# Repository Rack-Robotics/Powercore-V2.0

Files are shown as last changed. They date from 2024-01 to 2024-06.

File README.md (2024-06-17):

# Powercore V2.0

Powercore Front View 

The Powercore V2.0 is an open-source wire EDM (electrical discharge machining) power supply developed by Rack Robotics. It aims to provide a cost-effective and easily replicable solution for wire EDM enthusiasts and professionals. The project includes detailed electrical schematics, firmware, and CAD models. This EDM power supply (spark generator) is intended to be used on custom wire EDM and plunge EDM machines. 

This porject is open-source, to encourage collaboration and innovation within the wire EDM community.

## Powercore V2.0 Specifications

| Specification | Value |
|---|---|
| Typical Input Power | 200 Watts |
| Input Voltage | 90-264 VAC |
| Input Frequency | 47-63 Hz |
| Output Voltage | 65 VDC |
| Power Efficiency | Up to 90% |
| PSU Enable Port Voltage Input | 5-36 V |
| Physical Dimensions (XYZ) | 97 x 224 x 79.5 (mm) |

## Features 
- Firmare optimized for stable wire EDM opperation
- Up to 180 Watts EDM Power Output (Output Port)
- Up to 18 mJ per EDM spark
- 2 KHz EDM cutting with factory firmware
- Dual-core RP2040 Microcontroller up to 133 MHz (USB Port)
- Real-Time Current Sensing Telemetry (AMP Port) 
- Real-Time Spark Ignition Telemetry (ALRT Port) 
- External PSU Enable Safety Feature

## FAQ
**Can this cut X material?**

EDM can errode any conductive material. The rate of EDM (Electrical Discharge Machining) machining, also known as spark erosion, is significantly influenced by the thickness, melting point, and density of the material being worked on. Thicker materials generally require more time to erode due to the increased volume that must be removed. Materials with a higher melting point also slow down the machining rate as more energy is required to melt and vaporize the material at the spark point. Additionally, denser materials resist erosion more effectively, requiring more discharge energy to achieve the same material removal rate as less dense materials. Example feedrates are provided bellow, for 0.3 mm diameter zinc-coated, hard brass wire.

| Material | Example Feedrate |
|---|---|
| 3 mm Aluminum | 10 - 28 mm/min |
| 19 mm Aluminum | 1.6 - 4.4 mm/min |
| 4.75 mm Aluminum | 6 - 17 mm/min | 

**Can the Powercore V2.0 be used for sinker/plunge EDM?**

Yes. Gap control is highly recommended for sinker/plunge applications. In plunge/sink EDM, gap control is critical for maintaining machining stability. The gap, or spark gap, is the small space between the electrode and the workpiece. Proper gap control ensures consistent sparking conditions, preventing short circuits and arcing that can damage the workpiece and electrode. It also aids in efficient debris removal, cooling, and flushing of the dielectric fluid, which are essential for maintaining a smooth surface finish and achieving high-accuracy machining. Without precise gap control, the machining process can become unstable, leading to poor-quality results and increased wear on the electrodes. The Powercore V2.0 has a current sense and short alert output port to assist the user in thier implementation. 

## IO Ports

| Port | Description |
| --- | --- |
|**POWER** | The Powercore V2.0 outputs EDM waveforms through an 8-position Molex Micro-Fit 3.0 connector. The included output cable is 1 meter long and rated for 30 cycles. This cable consists of four twisted pairs to significantly reduce electromagnetic emissions. For more information about twisted wires and their benefits, refer to the best practices section.|
|**ALRT** | The Powercore V2.0 provides digital telemetry on the spark ignition rate via the ALRT port. The spark ignition rate, defined as the ratio of 'observed discharges' to 'possible discharges'. The spark ignition rate is a key indicator of feedrate efficiency. A low rate suggests the feedrate can be increased, while a high rate indicates an excessive feedrate or a short circuit. Telemetry is reported as a PWM duty cycle, which can be read by a control board or microcontroller. This port enables closed-loop feedrate control, ensuring optimal material removal. An ignition rate of approximately 80% has been observed to be optimal.|
|**AMP**| The Powercore V2.0 provides analog telemetry via the on-board current sensor (U17A, LMV358AIDGKR, output shunt). It is mapped to between 0V and 3.3V, at a rate of 12 mV/A. This may be used for closed-loop feedback control and debugging. |
|**EN**| The Powercore V2.0 features an "enable port" that ensures safety by requiring activation before the device outputs EDM waveforms. When the Powercore is plugged in, it remains inactive until the enable port receives a DC voltage between **5V and 36V**. This port draws minimal current. The enable port can be connected to GPIO, motor, heater, or LED ports on a 3D printer or CNC control board, or controlled manually with a switch. *To prevent damage*, avoid disconnecting the main AC power while the enable port is active.|
|**USB**| A type-C USB port provides communication with the on-board RP2040 micronctroller and flash memory. Pressing the reset button (the pin-hole located between the ‘AMP’ and ‘EN’ ports) during power-up initiates the USB bootloader mode, allowing access to the flash memory. When the reset button is held down while powering up, the RP2040 enters a special state where it presents itself as a mass storage device to a connected computer. This enables users to drag and drop firmware files directly into the flash memory, facilitating easy updates and modifications without needing additional programming tools or interfaces.|

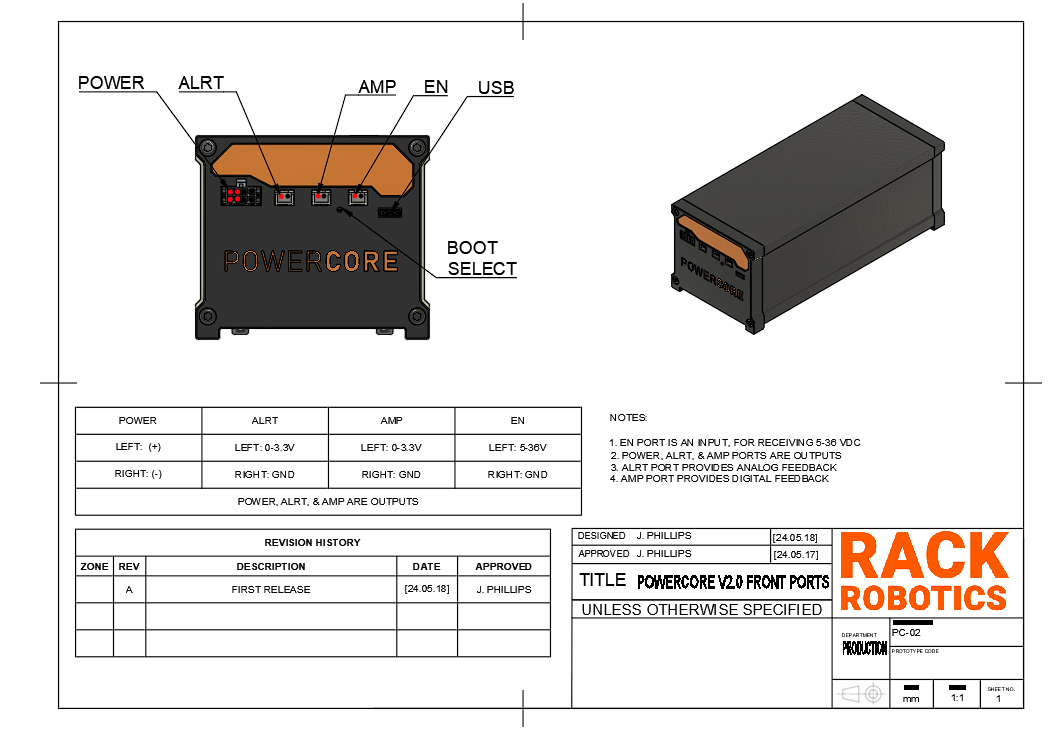
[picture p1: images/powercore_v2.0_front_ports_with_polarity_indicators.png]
Powercore Front View


**Best_Practices**

- Avoid short circuits. A short circuit occurs when the POWER port outputs short together. This may happen if wiring is incorrect, or the cutting electrode collides with the work. A prolonged short circuit can damage the Powercore.
- Twist the output power cable pairs together. Twisting the positive and negative output conductors together dramatically reduces EMI, and improves the cutting efficiency of the device. Output cables come twisted from Rack Robotics.
- When integrating the Powercore V2.0 into a wire EDM build, ensure that the EN port fails to an off default state during machine shutoff.
  
⚠ Avoid touching the electrodes and workpiece during operation to prevent exposure to high-voltage DC (65V). Additionally, individuals with pacemakers or similar medical devices should not operate the Powercore, as the high-voltage environment could interfere with their functionality. 

# Hardware Overview

The Powercore V2.0 contains a custom SMPS and motherboard. The internal SMPS is rated for 300 W typical and 550 watts peak, and accepts a range of AC voltages and frequencies. The SMPS provides 72 VDC to the motherboard, via the motherboard input supply connector (J1). The motherboard converts the steady 72 VDC input power, into pulsed high-current DC power, which is suitable for EDM.

**Theory of Operation**

The Powercore V2.0 motherboard delivers parametric pulsed DC through the repeated charging and discharging of a 32.9 µF capacitor bank. Efficient and rapid capacitor charging is achieved via a [peak current-mode control](https://www.ti.com/lit/ab/sboa187e/sboa187e.pdf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) (PCMC) *charger stage*. The onboard RP2040 *microcontroller* monitors the capacitor voltage and adjusts the PCMC charger parameters accordingly. When an output pulse is needed, the RP2040 discharges the capacitor bank through the MOSFET-driven *output stage* into the POWER port. This design allows for precise control over the EDM output pulse parameters: on-time, off-time, and peak voltage.

⚠ Adjustment of the firmware, including the on-time, off-time, and peak-voltage, may lead to damage of the PCMC switching converter. Do so at your own risk. 

**Motherboard**

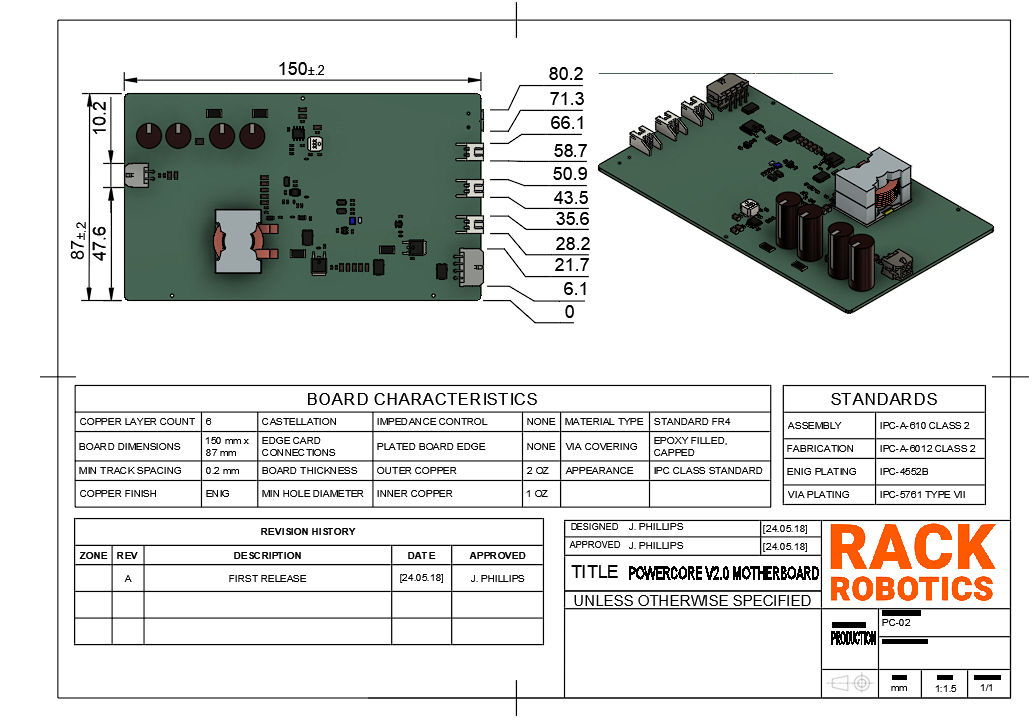
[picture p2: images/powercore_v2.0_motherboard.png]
Powercore Front View


The motherboard contains multiple functional blocks: 

- RP2040 Microcontroller with 16Mbit of FLASH Memory
- EMI Filter
- 72 VDC to 12 VDC Buck Converter
- 12 VDC & 5 VDC LDO
- Peak Current Detector
- Limit PWM Filter
- V_SENSE Scaler + Filter
- Peak Capacitor Voltage Trigger
- Constant Current PWM Generator
- Constant Current Limit Compensator & Slope Generator
- Output Curretn Sensor
- Charger Power Stage
- Output Stage

## Firmware Overview
Work in Progress

## Safety

DANGER The Powercore V2.0 operates at a potentially hazardous voltage of 65 - 72 VDC, and supplies high-power waveforms

Improper use of the Powercore can increase radiated emission levels. These intrinsic properties of EDM necessitate operator care and supervision. Touching the workpiece or electrode(s) during EDM operation exposes the may expose the user to 65 - 72 VDC high-voltage. Individuals with pacemakers or similar medical devices should not operate the Powercore, as the high-voltage environment could interfere with their functionality. Ensure that proper measures are taken against EMI. Routing of EDM power through unshielded/twisted cables not recommended. Unshielded/twisted cables function as antennas, which will radiate emissions into the nearby 

## 6. Legal & License

Shield: [][cc-by-nc]

This work is licensed under a
[Creative Commons Attribution-NonCommercial 4.0 International License][cc-by-nc].

[][cc-by-nc]

[cc-by-nc]: https://creativecommons.org/licenses/by-nc/4.0/
[cc-by-nc-image]: https://licensebuttons.net/l/by-nc/4.0/88x31.png
[cc-by-nc-shield]: https://img.shields.io/badge/License-CC%20BY--NC%204.0-lightgrey.svg

You are free to:
- Share — copy and redistribute the material in any medium or format
- Adapt — remix, transform, and build upon the material

Under the following terms:
- Attribution — You must give appropriate credit, provide a link to the license, and indicate if changes were made. You may do so in any reasonable manner, but not in any way that suggests the licensor endorses you or your use.
- NonCommercial — You may not use the material for commercial purposes.

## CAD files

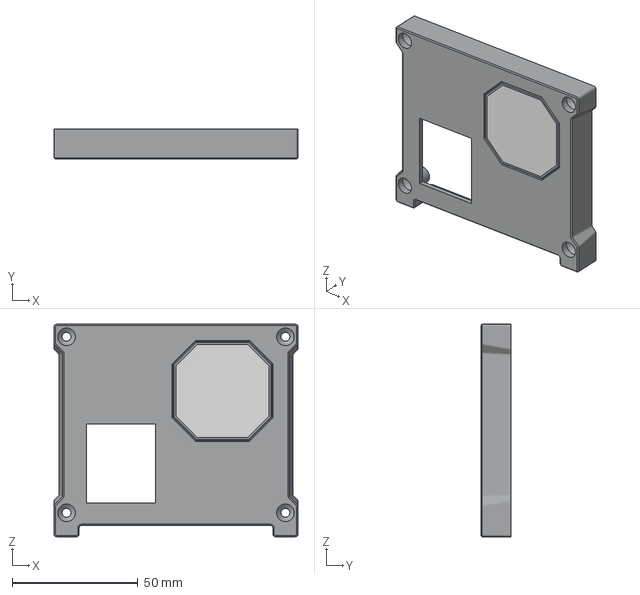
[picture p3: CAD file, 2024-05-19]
Powercore-V2.0 CAD/Back Panel v18.3mf
97.0 x 12.0 x 84.5 mm

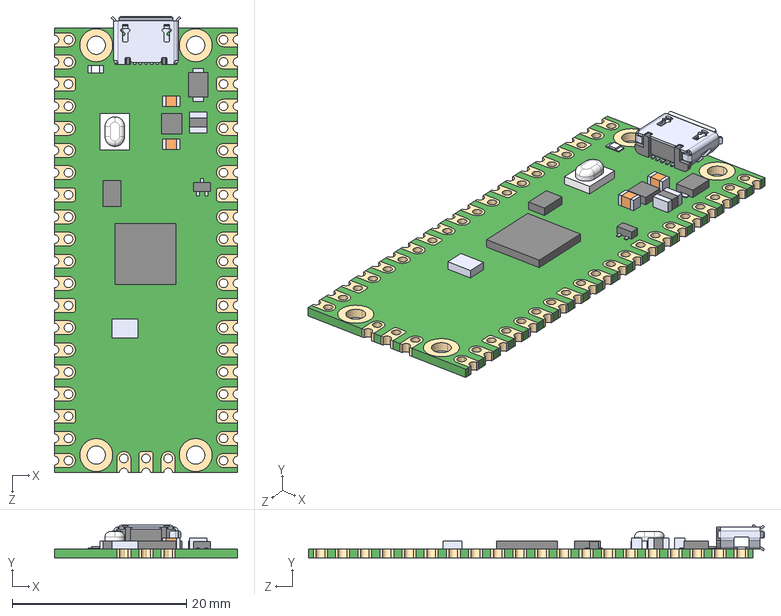
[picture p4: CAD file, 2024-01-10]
Powercore-V2.0 Motherboard/KiCAD/KiCAD Libraries/3dmodels/MCU_MODULES/SC0915.step
21.0 x 3.73 x 52.3 mm

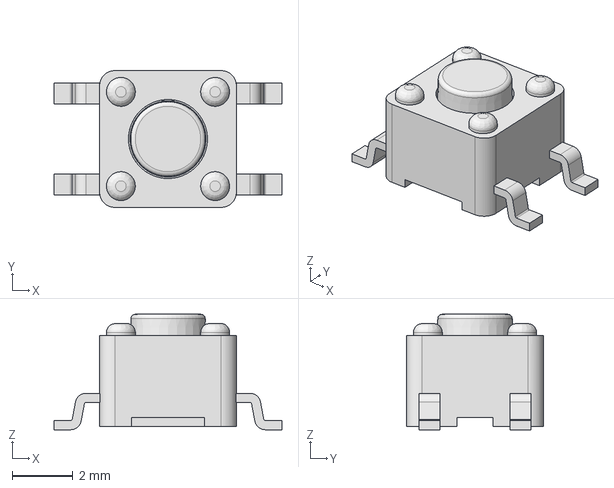
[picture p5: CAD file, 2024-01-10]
Powercore-V2.0 Motherboard/KiCAD/KiCAD Libraries/3dmodels/SWITCHES/TL3305AFxxxxG.stp
7.50 x 4.50 x 3.80 mm

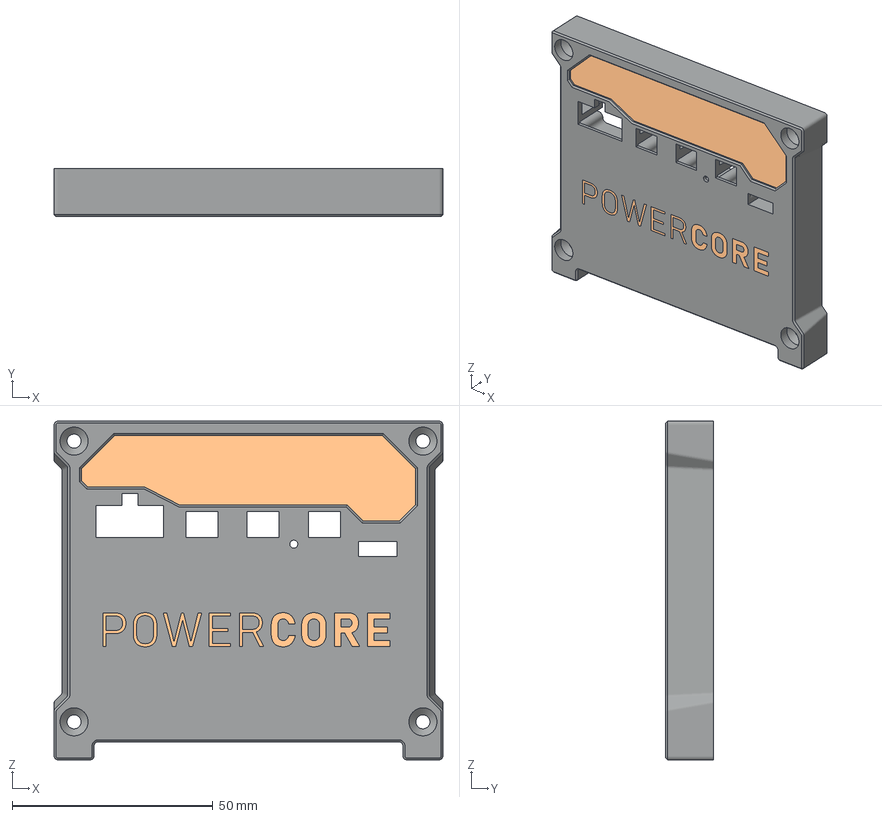
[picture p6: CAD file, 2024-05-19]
Powercore-V2.0 CAD/Front Panel v45.3mf
97.0 x 12.0 x 84.5 mm

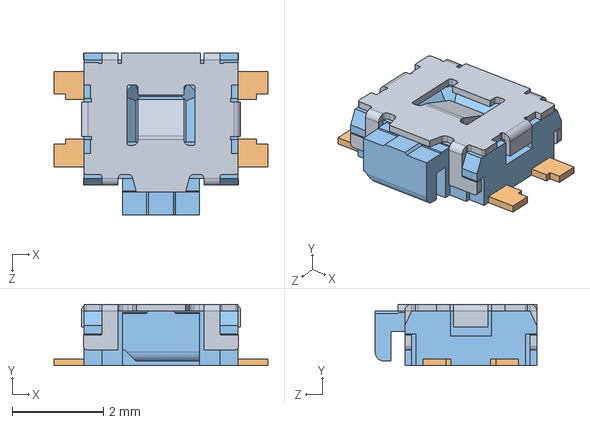
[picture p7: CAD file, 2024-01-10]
Powercore-V2.0 Motherboard/KiCAD/KiCAD Libraries/3dmodels/SWITCHES/EVQ-P7A01P.step
4.70 x 1.35 x 3.55 mm

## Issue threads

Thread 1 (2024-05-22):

Please add a EEVblog discussion thread

myjtag, 2024-05-22:
Hi
I highly recommend that you make a thread on EEVblog  forum, because there are lot's of interaction and highly skilled engineers there, to contribute and give feedback, Also I recommend you choose a better equipped MCU with SMPS control peripherals like STM32G431CBT6 which is affordable  enough and have lot's of great peripherals for controlling Advanced SMPS circuits. like ADC, DAC, Op-amp , comparator and Cordic engine

John-RackRobotics, 2024-05-29:
While I am a fan of the EEVblog YouTube channel, I do not frequent the forum. For our application, we do not require the STM32G431CBT6. We are happy with the RP2040 for the Powercore V2.0.

myjtag, 2024-05-30:
I highly recommend making a thread there, there is a hug and very active community there, they would help and contribute a lot.

Closed 2024-05-30.

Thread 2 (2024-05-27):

Is description of U2 in BOM correct

alberto-simoes, 2024-05-27:
Hi just checking the description of U2 in the BOM should read RP204... and not what it shows currently SC0914?

Apologies if i've misunderstood something here.

John-RackRobotics, 2024-05-29:
SC0914(13) is the original manufacturer part number for the RP2040 MCU, produced by Raspberry Pi.

Closed 2024-05-29.

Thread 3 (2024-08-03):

it stay in boot from flash mode

atmelletje, 2024-08-03:

atmelletje, 2024-08-03:
I build the board according to your designs, I don't have to push the boot button as it stays in boot mode. I used the MCU from an rp pico. all other parts are new. I meassure 3.25v at CLR pin 1. boot switch removed makes also no difference.

atmelletje, 2024-08-03:
that problem is solved. it was a fake/broken Flash chip.

Closed 2025-05-05.

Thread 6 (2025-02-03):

How to connect the internal circuit board of powercore V2

Logan147, 2025-02-03:
Thank you for your open source, sir, you are a genius！！！
Below is my question
1. Does powercore V2 need a resistor board like the V1 version, and how to connect the various internal circuit boards?
2. Can you provide a further detailed wiring diagram?

Logan147, 2025-02-03:
For example, how to connect the SMP power supply to the motherboard and the cooling fan?

Logan147, 2025-02-03:
For example, how to connect the SMPS power supply to the motherboard and the cooling fan?

Logan147, 2025-02-07:
ok, i got it.

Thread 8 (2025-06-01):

Control stage

hinell, 2025-06-01:
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

First of all: thanks for great project. I'm trying to figure out what these two OP-amps are doing in control stage. Why no output? Where I can read more about this?

Is this paper on [Current Mode Control in Switching Power Supplies](https://www.ti.com/lit/ab/sboa187e/sboa187e.pdf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) relatd to the the said op-amps?

Thanks!

Closed 2025-06-14.

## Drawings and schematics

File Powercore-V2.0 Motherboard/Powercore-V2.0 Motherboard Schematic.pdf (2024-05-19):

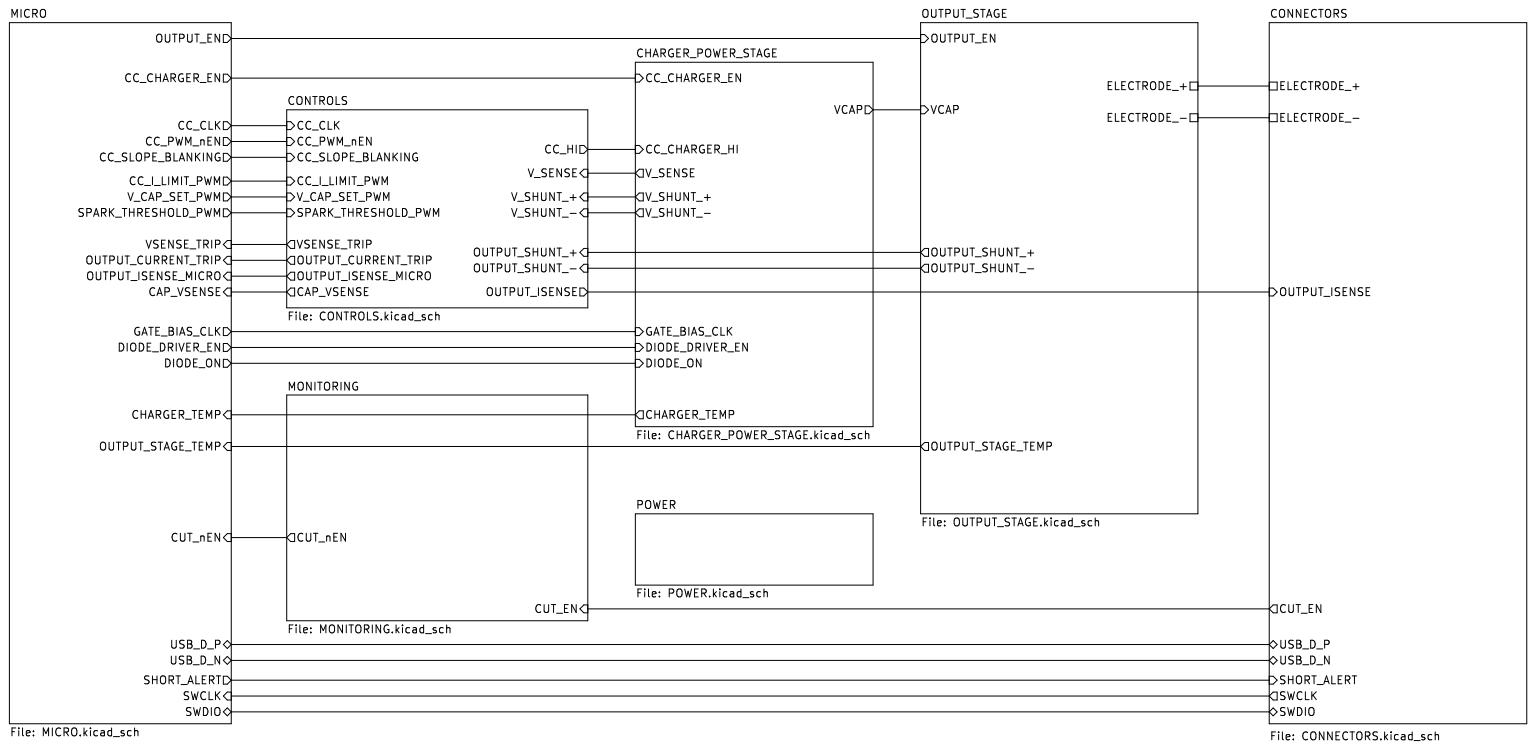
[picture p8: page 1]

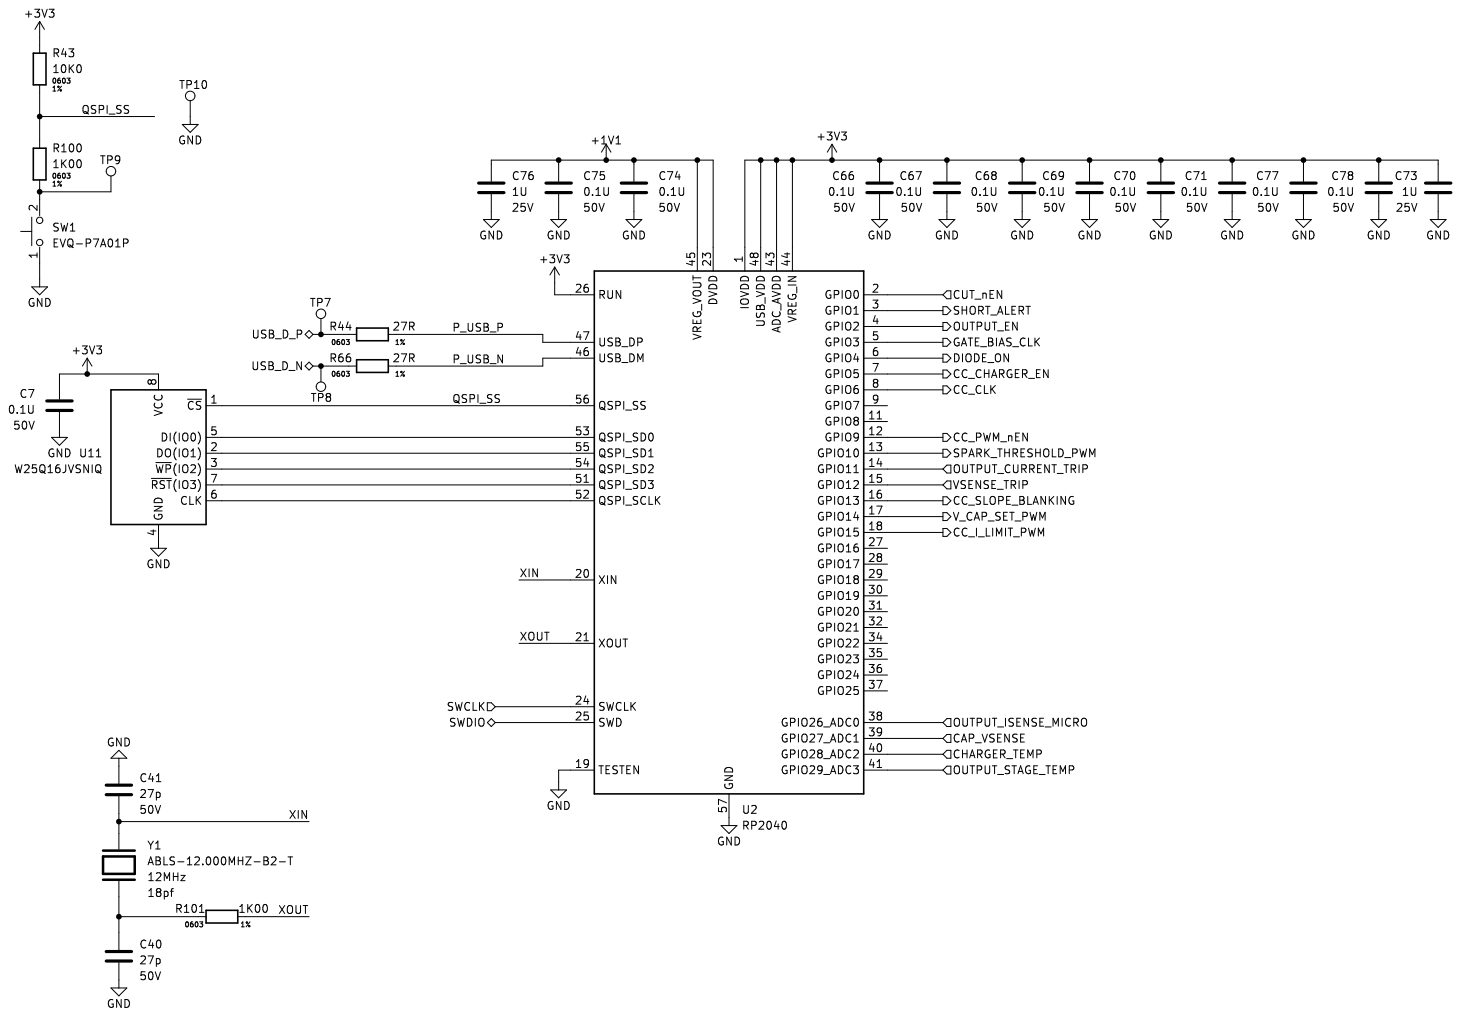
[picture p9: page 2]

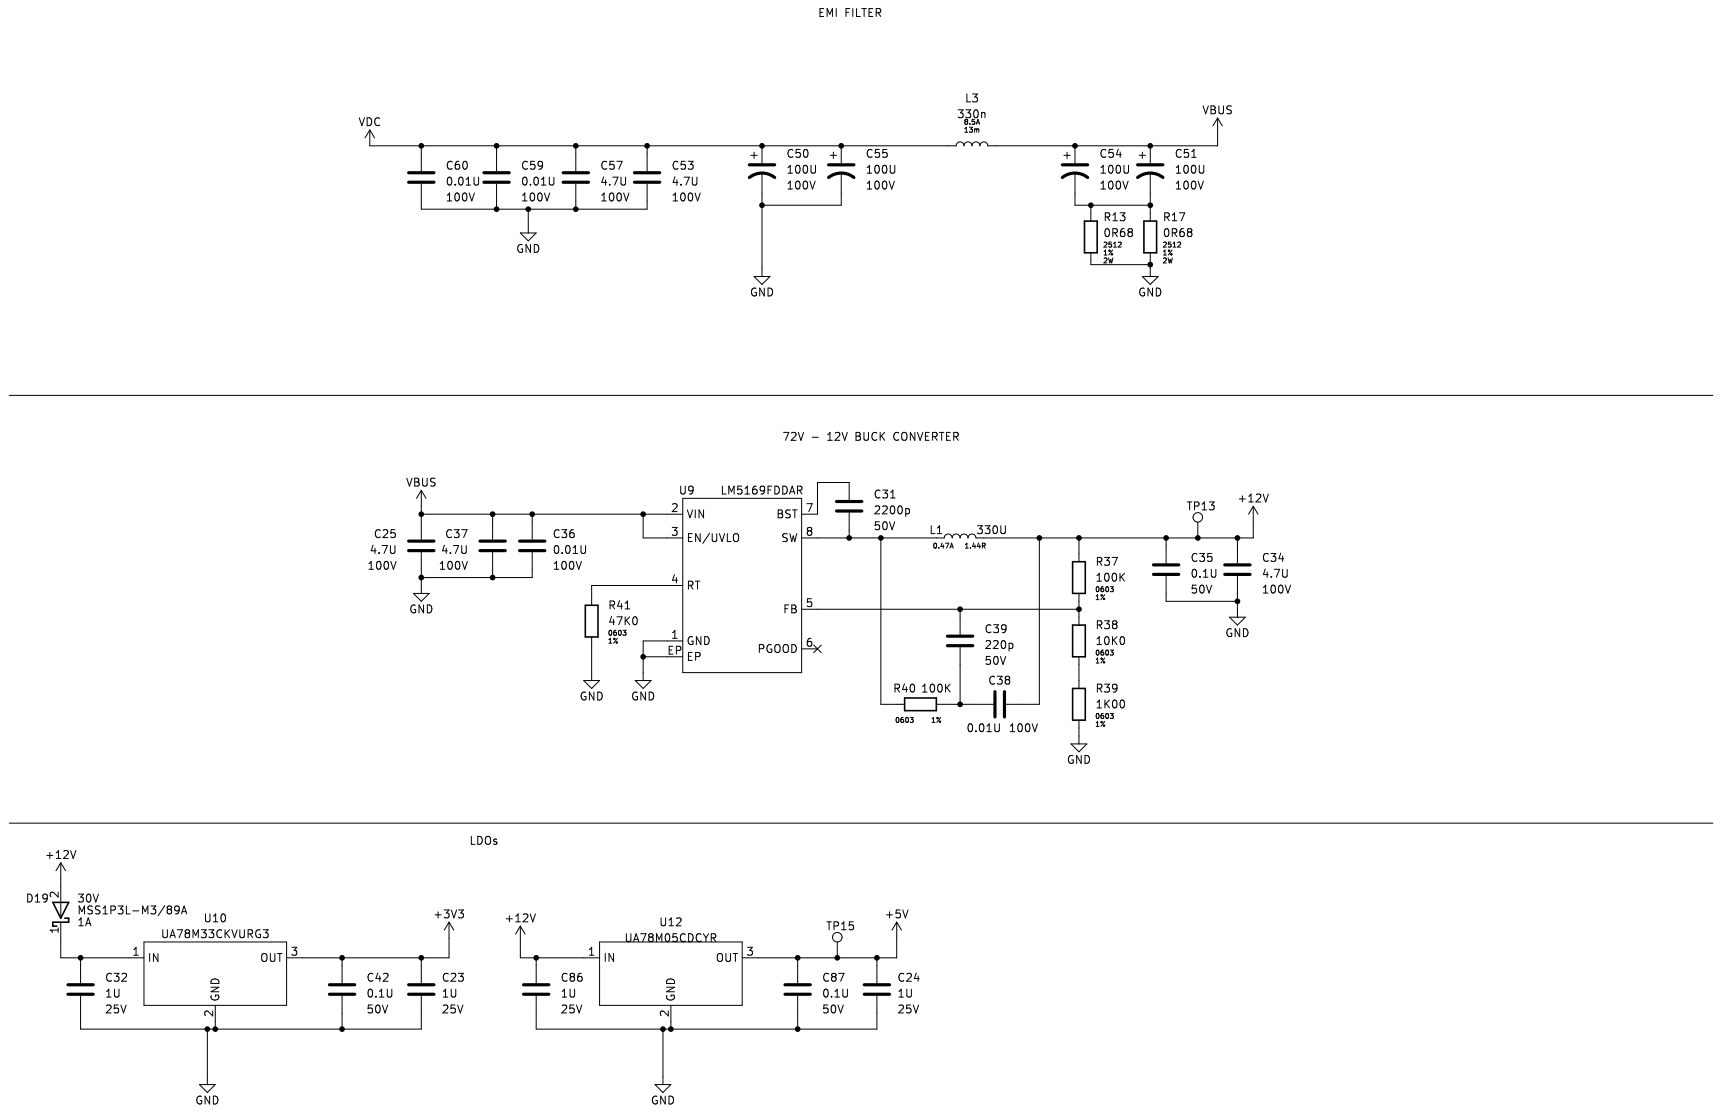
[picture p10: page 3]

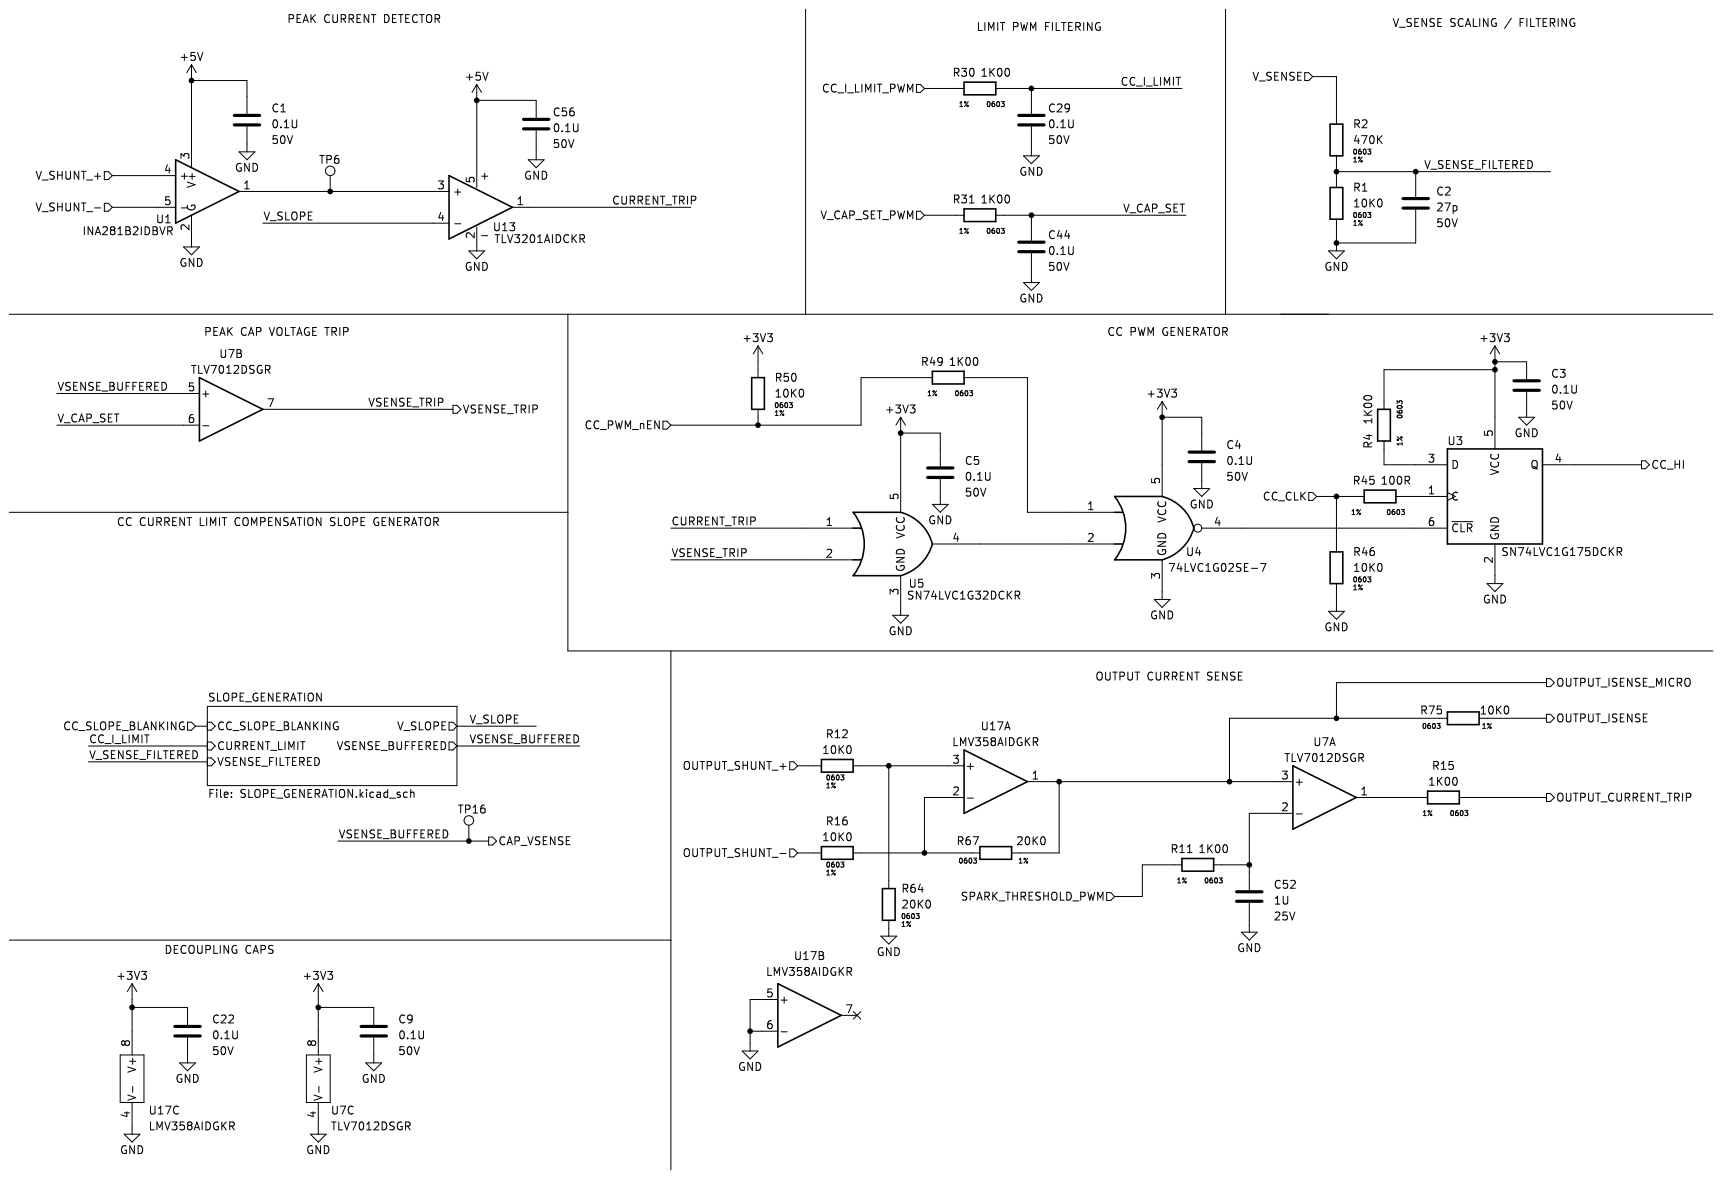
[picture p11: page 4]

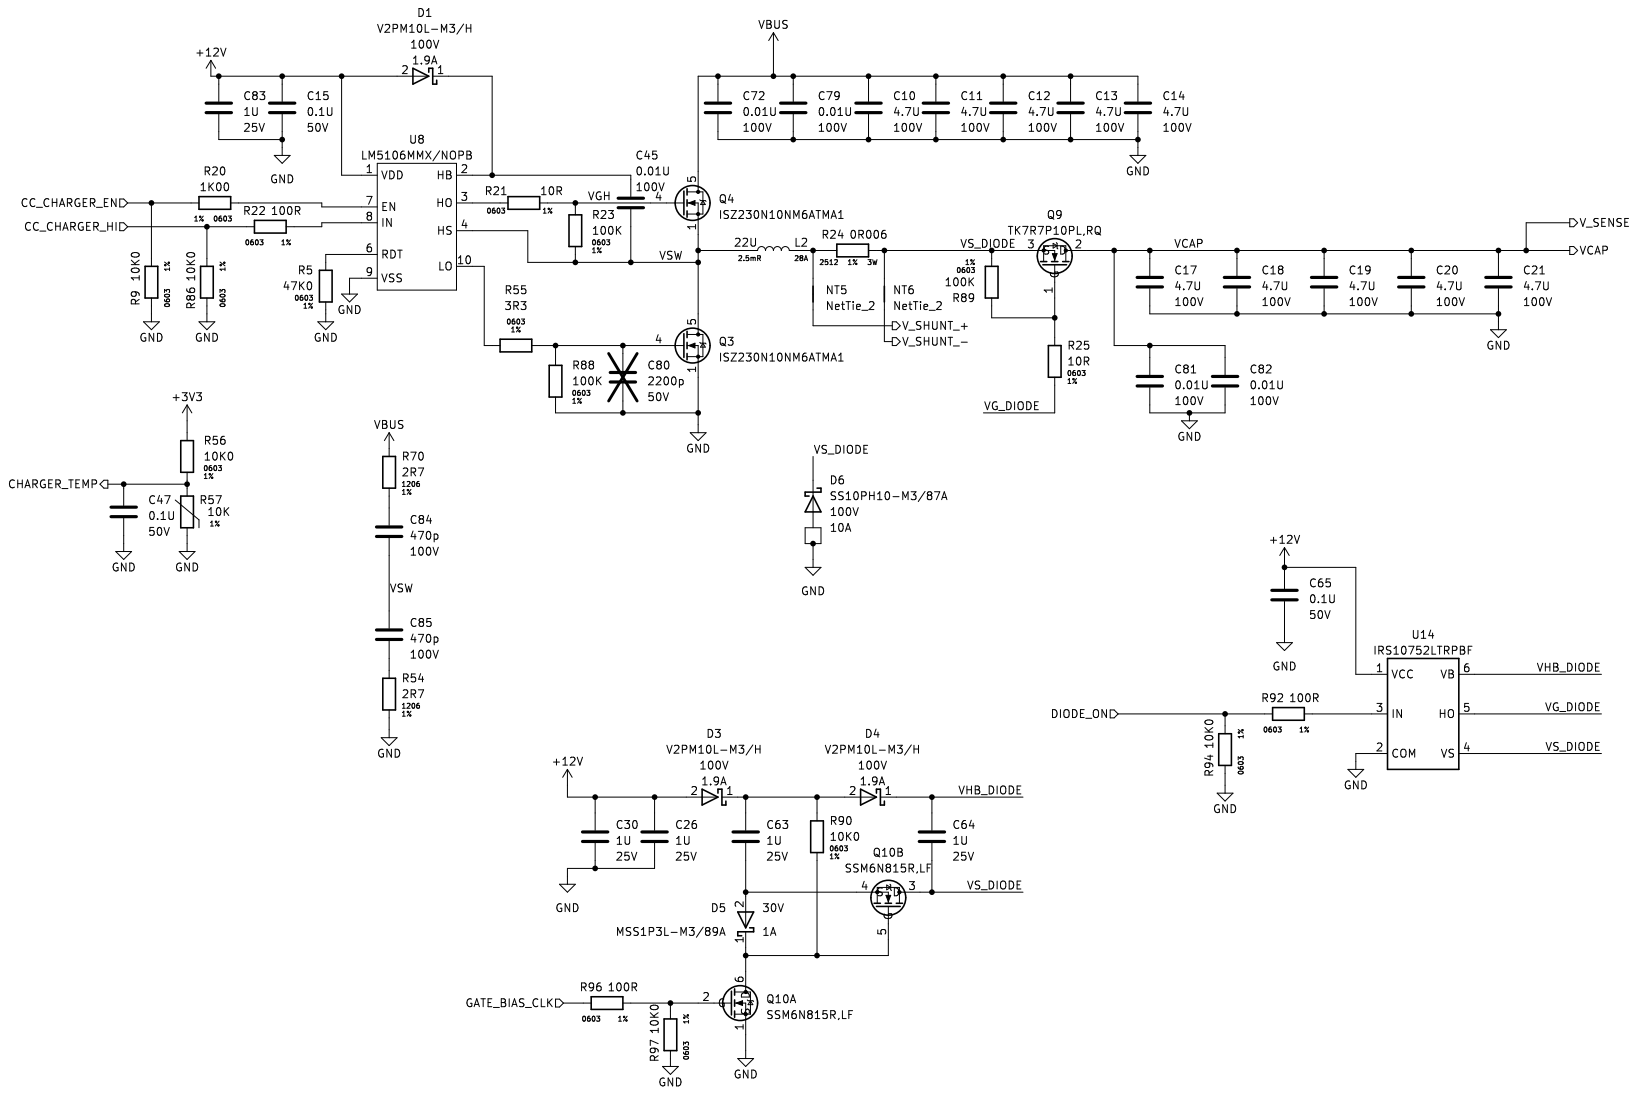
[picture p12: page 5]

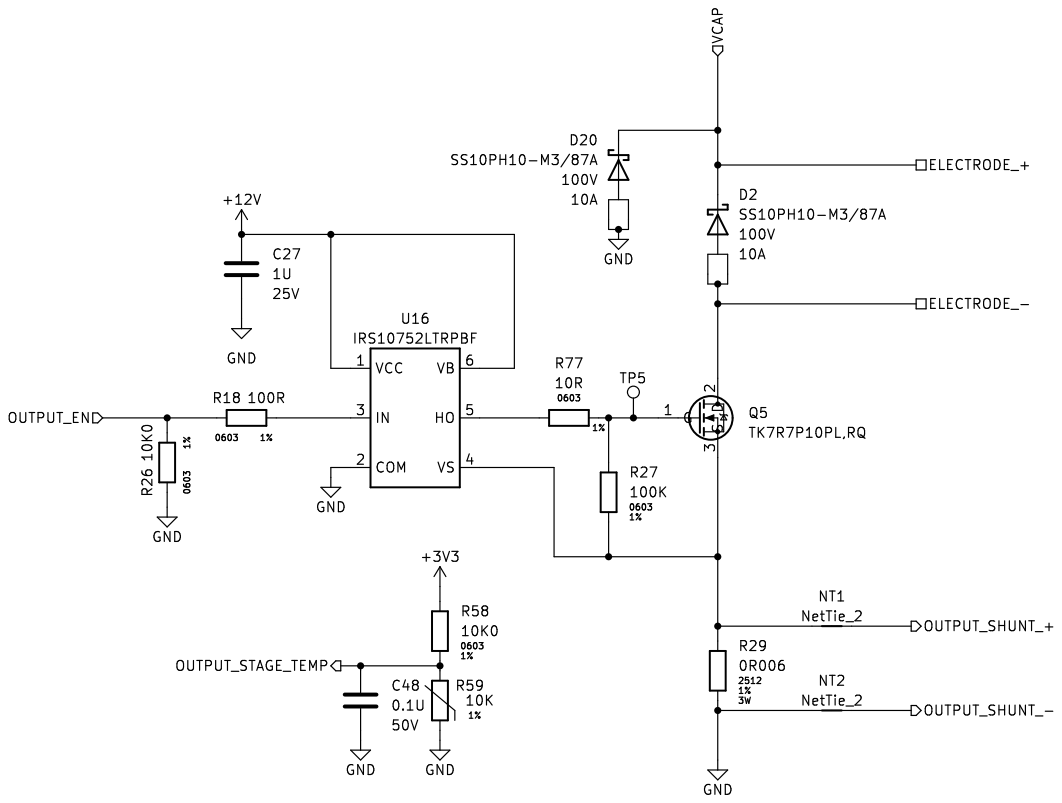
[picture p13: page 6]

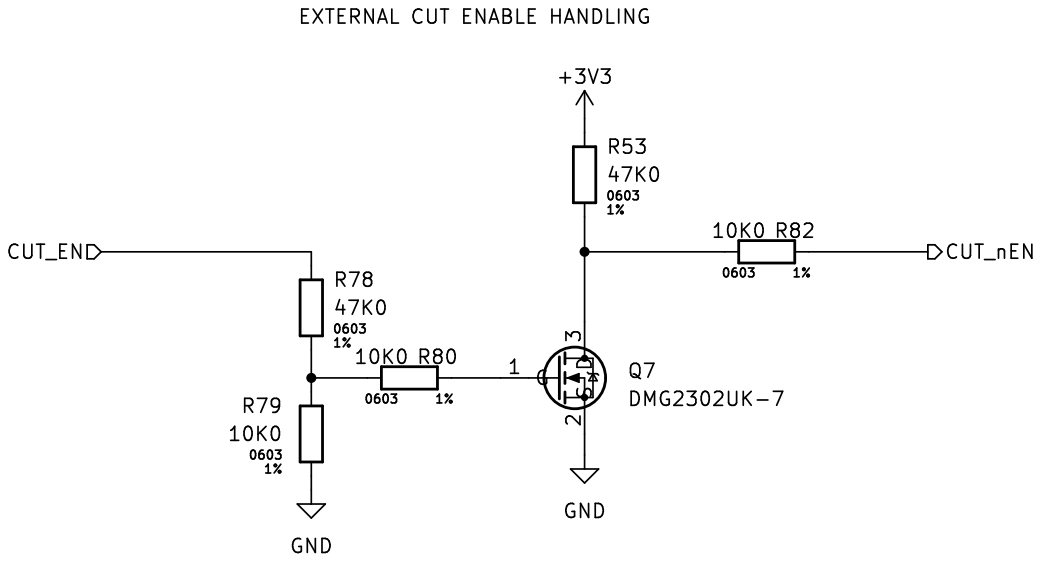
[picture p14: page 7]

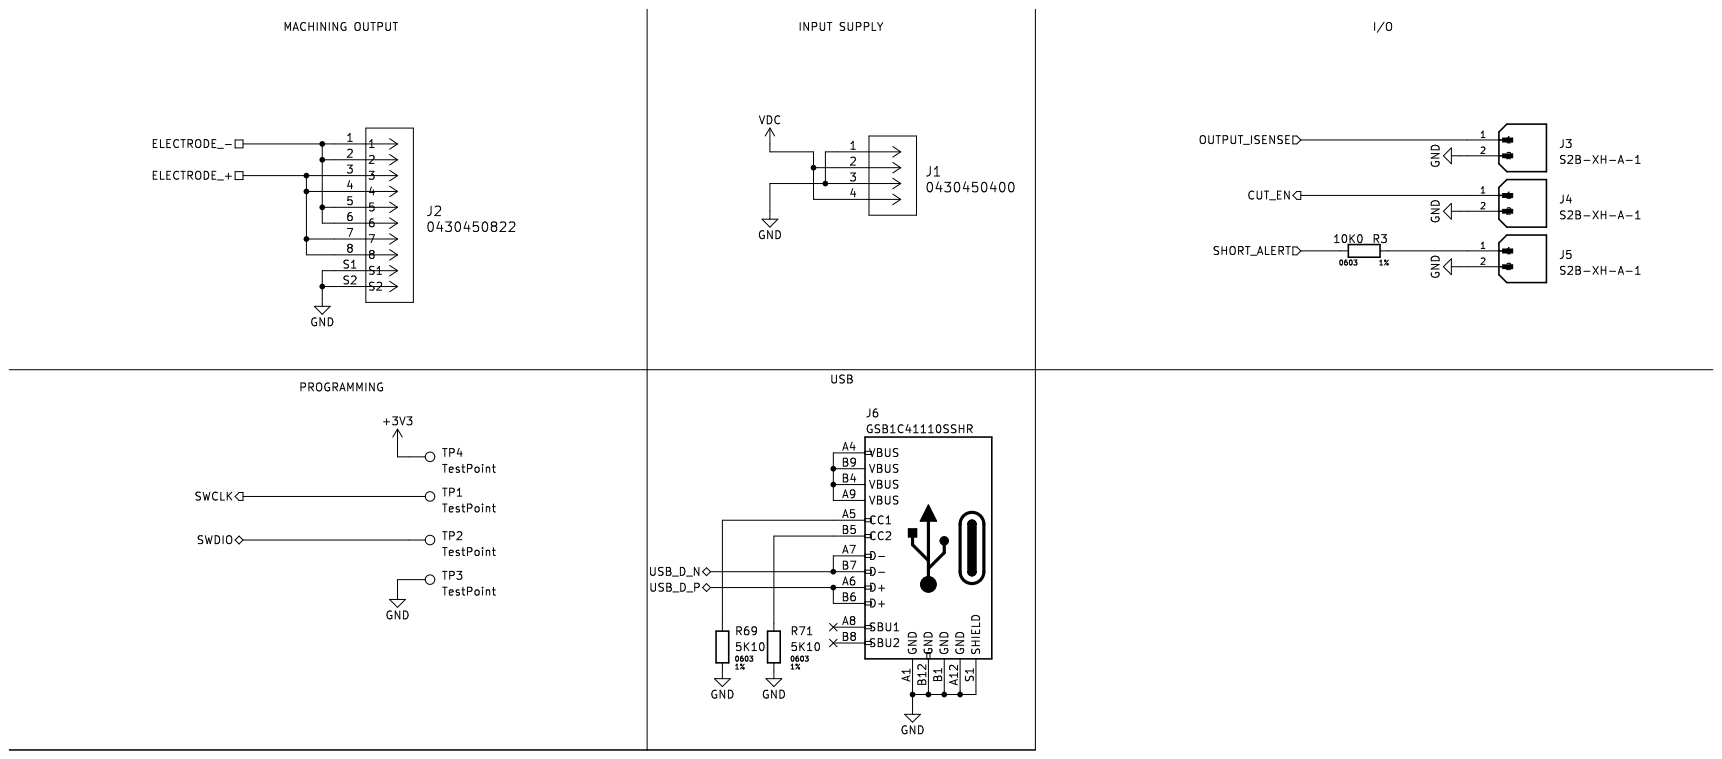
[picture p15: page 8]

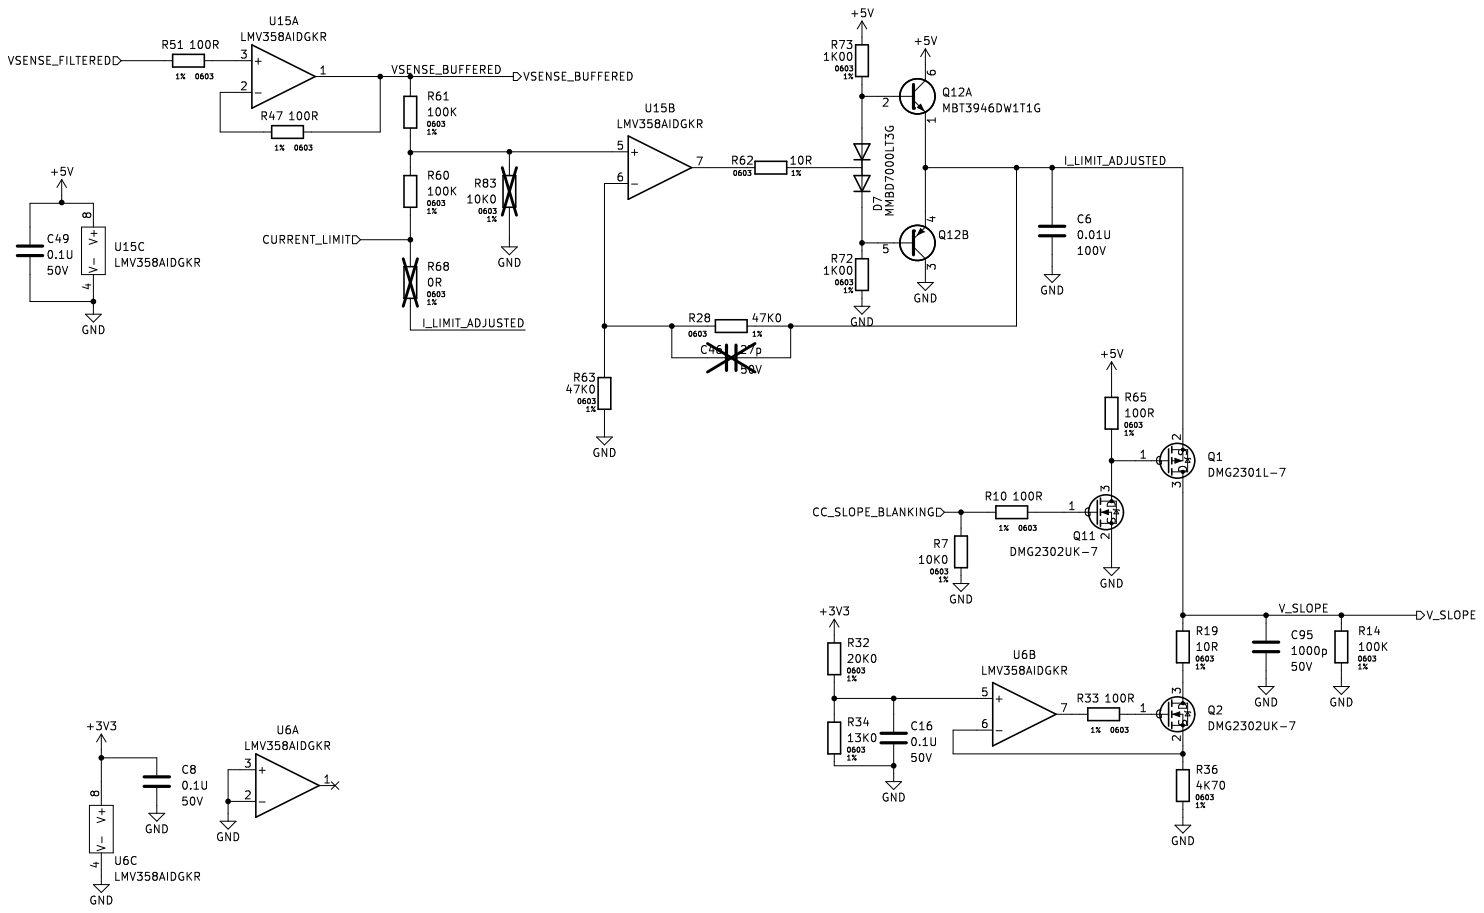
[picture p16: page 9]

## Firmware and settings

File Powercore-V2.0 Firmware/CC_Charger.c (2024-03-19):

#include "pico/stdlib.h"
#include "hardware/pio.h"
#include "hardware/pwm.h"
#include "CC_Charger.h"
#include "hardware/adc.h"

// Our assembled programs:
#include "CLK.pio.h"
#include "TIMING.pio.h"

//Pinout Definitions

//CC_Charger Timing:
#define CLK_PIN 6
#define LIMIT_PIN 9
#define BLANKING_PIN 13

//CC_Charger Control:
#define CC_CHARGER_EN_PIN 5

//Ideal Diode Controls:
#define DIODE_ON_PIN 4

//Gate Bias PWM:
#define GATE_BIAS_CLK_PIN 3

//PWM Voltage Sets:
#define CC_I_LIMIT_PIN 15
#define V_CAP_SET_PIN 14

//Telemetry:
#define VSENSE_TRIP_PIN 12

PIO pio;

int sm, sm_clk, sm_limit, sm_blanking;
uint offset_clk, offset_timing;

uint32_t default_clk_period         = 133;                                                      //3.216usec
uint32_t default_limit_wait_time    = 185;                                                      //3.024usec
uint32_t default_limit_on_time      = 7;                                                        //0.136usec
uint32_t default_blanking_wait_time = 185;                                                      //0.112usec
uint32_t default_blanking_on_time   = 12;                                                       //3.032usec

bool caps_charged = false;

void VSENSE_TRIP_callback(void) {

    if(gpio_get_irq_event_mask(VSENSE_TRIP_PIN) & GPIO_IRQ_EDGE_RISE) {
        
        gpio_acknowledge_irq(VSENSE_TRIP_PIN, GPIO_IRQ_EDGE_RISE);

        //Flag that the caps have been charged
        caps_charged = true;

        //Turn off the CC_Charger
        disable_CC_timing();
    }

    if(gpio_get_irq_event_mask(VSENSE_TRIP_PIN) & GPIO_IRQ_EDGE_FALL) {
        
        gpio_acknowledge_irq(VSENSE_TRIP_PIN, GPIO_IRQ_EDGE_FALL);

        //Flag that the caps are not fully charged
        caps_charged = false;

    }

}

void disable_gate_driver() {
    gpio_put(CC_CHARGER_EN_PIN, false);
}

void disable_CC_timing() {

    gpio_put(DIODE_ON_PIN, false);                                                              //Turn off ideal diode

    pio_sm_set_enabled(pio, sm_clk, false);                                                     //Disable CC Charger Clock
    pio_sm_exec(pio, sm_clk, pio_encode_nop() | pio_encode_sideset_opt(1, 0));                  //Set Clock output to 0
    pio_sm_exec(pio, sm_clk, pio_encode_irq_set(false, 0));

    pio_sm_set_enabled(pio, sm_limit, false);                                                   //Disable PWM limit SM
    pio_sm_exec(pio, sm_limit, pio_encode_nop() | pio_encode_sideset_opt(1, 1));                //Set PWM limit to 1 (keeps !CLR on Flip Flop low)

    pio_sm_set_enabled(pio, sm_blanking, false);                                                //Disable Slope blanking/reset 
    pio_sm_exec(pio, sm_blanking, pio_encode_nop() | pio_encode_sideset_opt(1, 1));             //Set Slope blanking to  (Allows the compensated current limit to decay to 0)

}

void enable_CC_timing(bool diode_on) {

    //Don't start the charger if the caps are already charged
    if(caps_charged == false){

        //Reset all PIOs to the start of the program:
        pio_sm_exec(pio, sm_clk,        pio_encode_jmp(offset_clk   ));
        pio_sm_exec(pio, sm_blanking,   pio_encode_jmp(offset_timing));
        pio_sm_exec(pio, sm_limit,      pio_encode_jmp(offset_timing));

        //Renable PIOs
        pio_sm_set_enabled(pio, sm_limit,       true);
        pio_sm_set_enabled(pio, sm_blanking,    true);
        pio_sm_set_enabled(pio, sm_clk,         true);

        gpio_put(CC_CHARGER_EN_PIN, true);                                                      //Enable the CC Charger gate driver

        gpio_put(DIODE_ON_PIN, diode_on);                                                           //Turn on the ideal diode
    }

}

void CLK_set_period(uint32_t period) {

    pio_sm_put_blocking(pio, sm_clk, period);                                                   //Load new period into FIFO
    pio_sm_exec(pio, sm_clk, pio_encode_pull(false, false));                                    //Pull new period into OSR
    pio_sm_exec(pio, sm_clk, pio_encode_out(pio_isr, 32));                                      //Shift new period from OSR to ISR

    pio_sm_put_blocking(pio, sm_clk, period/2);                                                 //Load new on time into FIFO        
    pio_sm_exec(pio, sm_clk, pio_encode_pull(false, false));                                    //Pull new on time into OSR
    pio_sm_exec(pio, sm_clk, pio_encode_out(pio_x, 32));                                        //Shift new on time into X register

}

void SM_set_timing(PIO pio, uint sm, uint32_t wait_time, uint32_t on_time, bool enabled) {

    pio_set_sm_mask_enabled(pio, sm_clk | sm_blanking | sm_limit, false);
    // pio_sm_set_enabled(pio, sm, false);                                                      //Temporarily freeze SM

    pio_sm_put_blocking(pio, sm, wait_time);                                                    //Load new wait time into FIFO
    pio_sm_exec(pio, sm, pio_encode_pull(false, false));                                        //Pull new wait time into OSR
    pio_sm_exec(pio, sm, pio_encode_out(pio_isr, 32));                                          //Shift new wait time into ISR
    
    pio_sm_put_blocking(pio, sm, on_time);                                                      //Load new on time into FIFO
    pio_sm_exec(pio, sm, pio_encode_pull(false, false));                                        //Pull new wait time into OSR

    // pio_sm_set_enabled(pio, sm, enabled);                                                    //Renable SM
    pio_set_sm_mask_enabled(pio, sm_clk | sm_blanking | sm_limit, enabled);

}

void LIMIT_set_timing(uint32_t wait_time, uint32_t on_time, bool enabled) {

    SM_set_timing(pio, sm_limit, wait_time, on_time, enabled);                                  //Update timing registers in SM

}

void BLANKING_set_timing(uint32_t wait_time, uint32_t on_time, bool enabled) {

    SM_set_timing(pio, sm_blanking, wait_time, on_time, enabled);                               //Update timing registers in SM

}
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

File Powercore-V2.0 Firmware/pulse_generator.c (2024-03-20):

#include "pico/stdlib.h"
#include "pulse_generator.h"
#include "CC_Charger.h"
#include "hardware/pwm.h"
#include "hardware/adc.h"

#define OUTPUT_EN_PIN 2
#define OUTPUT_CURRENT_TRIP_PIN 11
#define SPARK_THRESHOLD_PWM_PIN 10
#define SHORT_ALERT_PIN 1

#define CAP_VSENSE_PIN 27

#define SHORT_THRESHOLD 513

bool cutting_enabled = false;
bool short_tripped = false; 

//Enum to keep track of where we are in the pulse sequence
enum pulse_state{   WAITING_FOR_IGNITION,
                    SPARK_ON,
                    SPARK_OFF};

enum pulse_state output_state = SPARK_OFF;

//Pulse definition waveforms
uint32_t pulse_on_time      = 0;
uint32_t pulse_off_time     = 0;
bool     iso_pulse_mode     = false;
uint32_t pulse_timeout_time = 0; //time in us

alarm_id_t timeout_alarm_id;

//Pulse history tracking (512 cycles, 1 bit per cycle)
uint32_t pulse_history[16] = {0, 0, 0, 0, 0, 0, 0, 0, 0, 0, 0, 0, 0, 0, 0, 0};
uint32_t pulse_counter = 0;

//Prototype functions
int64_t begin_off_time(alarm_id_t id, void *user_data);

//Set the CC timing to the standard charging parameters
int64_t change_CC_timing(alarm_id_t id, void *user_data){

    LIMIT_set_timing(185, 7, true);

    return 0;

}

void short_alert_off() {

    pwm_set_gpio_level(SHORT_ALERT_PIN, 0);

}

void output_current_trip_irq(void) {

    if (gpio_get_irq_event_mask(OUTPUT_CURRENT_TRIP_PIN) & GPIO_IRQ_EDGE_RISE) {

        gpio_acknowledge_irq(OUTPUT_CURRENT_TRIP_PIN, GPIO_IRQ_EDGE_RISE);

        gpio_set_irq_enabled(OUTPUT_CURRENT_TRIP_PIN, GPIO_IRQ_EDGE_RISE, false);   //Turn off the interrupt on the ignition sense

        output_state = SPARK_ON;                                                    //Update the pulse generator state

        if(iso_pulse_mode == true){

            cancel_alarm(timeout_alarm_id);                                         //Turn off timeout alarm
            add_alarm_in_us(pulse_on_time, begin_off_time, NULL, true);             //Set alarm to turn off the pulse after the pulse on time

        }

    }

}

int64_t begin_on_time(alarm_id_t id, void *user_data){

    disable_CC_timing();                                                            //Turn off the CC Charger

    if(cutting_enabled) {                                                           //Check that cutting is still enabled
        
        output_state = WAITING_FOR_IGNITION;                                        //Update pulse generator state

        gpio_set_irq_enabled(OUTPUT_CURRENT_TRIP_PIN, GPIO_IRQ_EDGE_RISE, true);    //Configure detection of the spark

        if(iso_pulse_mode) {                                                        //Check pulse mode is iso-pulse
            
            timeout_alarm_id = add_alarm_in_us(pulse_timeout_time, begin_off_time, NULL, true);        //Set the alarm in case of pulse timeout

        } else {                                                                    //If pulse mode is iso-tonic

            add_alarm_in_us(pulse_on_time, begin_off_time, NULL, true);             //Set alarm for the off transition

        }

        gpio_put(OUTPUT_EN_PIN, true);                                              //Turn on output FET

    } else {

        gpio_put(OUTPUT_EN_PIN, false);

    }

    return 0;

}


int64_t begin_off_time(alarm_id_t id, void *user_data){

    gpio_put(OUTPUT_EN_PIN, false);                                                 //Turn off output MOSFET

    gpio_set_irq_enabled(OUTPUT_CURRENT_TRIP_PIN, GPIO_IRQ_EDGE_RISE, false);       //Disable the ignition sense irq

    LIMIT_set_timing(97, 7, false);                                             //Limit CC Charger PWM duty cycle to avoid inrush (was 97)

    enable_CC_timing(true);                                                             //Start CC Charger

    add_alarm_in_us(15, change_CC_timing, NULL, true);                          //Setup the alarm to correct CC charger timing
    add_alarm_in_us(pulse_off_time-11, begin_on_time, NULL, true);                  //Setup the alarm to turn on the output MOSFET after the off time

    pulse_counter -= pulse_history[0] & (uint32_t)0x1;                                          //Subtract the 512th pulse state from the counter

    for(int i = 0; i < 15; i++) {                                                        

        pulse_history[i] = ((pulse_history[i+1] & (uint32_t)0x1) << 31) + (pulse_history[i] >> 1);   //Binary shift the whole array (left shift each int and load in the first bit of the one above it)

    }

    pulse_history[15] = pulse_history[15] >> 1;                                       //Binary shift the last value, done outside the for loop because nowhere to pull the MSB from

    if(output_state == SPARK_ON) {                                                  //If successful spark then load a 1 into the MSB of the shift register and increment pulse counter

        pulse_history[15] = pulse_history[15] + (1 << 31);

        pulse_counter += 1;

    }

    output_state = SPARK_OFF;                                                       //Set state machine state to SPARK_OFF

    if(pulse_counter > SHORT_THRESHOLD) {
        cutting_enabled = false;
        short_tripped = true;
        disable_CC_timing();
        disable_gate_driver();
        pwm_set_gpio_level(SHORT_ALERT_PIN, 512);
    }else {
        pwm_set_gpio_level(SHORT_ALERT_PIN, pulse_counter);
    }

    return 0;

}

void first_off_time(){

    gpio_put(OUTPUT_EN_PIN, false);                                                 //Turn off output MOSFET

    gpio_set_irq_enabled(OUTPUT_CURRENT_TRIP_PIN, GPIO_IRQ_EDGE_RISE, false);       //Disable the ignition sense irq

    LIMIT_set_timing(97, 7, false);                                                 //Limit CC Charger PWM duty cycle to avoid inrush (was 97)

    enable_CC_timing(true);                                                             //Start CC Charger

    add_alarm_in_us(15, change_CC_timing, NULL, true);                              //Setup the alarm to correct CC charger timing
    add_alarm_in_us(pulse_off_time-11, begin_on_time, NULL, true);                  //Setup the alarm to turn on the output MOSFET after the off time

}

void begin_output_pulses(uint32_t on_time, uint32_t off_time, bool iso_pulse) {

    //Load in the pulse parameters
    pulse_on_time = on_time;
    pulse_off_time = off_time;
    pulse_timeout_time = pulse_on_time / 2;
    iso_pulse_mode = iso_pulse;

    for (int i = 0; i < 15; i++)
        pulse_history[i] = 0;
    pulse_counter = 0;

    first_off_time();

}
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

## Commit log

2024-01-10 Embedded libraries for all custom components
    Added DPS internal libraries to file structure to improve portability
    [0430450400.step, 430450822.stp, CAP_YX_10X20_RUB.step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]
2024-01-10 Fixed modified footprint references
    [CONNECTORS.kicad_sch]
2024-01-11 Finalized Design for 24/1/10 Order and Generated Manufacturing files
    [POWERCORE-V2.0_MOTHERBOARD-B_Cu.gbl, POWERCORE-V2.0_MOTHERBOARD-B_Mask.gbs, POWERCORE-V2.0_MOTHERBOARD-B_Paste.gbp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]
2024-01-11 Added no note version of gerbers
    Added a version of the gerbers w/o the drawings notes on each layer in case JLCPCB complains about it
    [POWERCORE-V2.0_MOTHERBOARD-B_Cu.gbl, POWERCORE-V2.0_MOTHERBOARD-B_Mask.gbs, POWERCORE-V2.0_MOTHERBOARD-B_Paste.gbp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]
2024-01-14 Generated pure Gerbers
    [POWERCORE-V2.0_MOTHERBOARD-B_Cu.gbl, POWERCORE-V2.0_MOTHERBOARD-B_Mask.gbs, POWERCORE-V2.0_MOTHERBOARD-B_Paste.gbp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]
2024-01-28 Firmware Update
    Firmware updated with appropriate pinouts for Rev3 boards. Timings also accelerated to
2024-01-29 Fixed EN signal issues
    Glitchy/bouncy inputs to the EN pin were previously causing two versions of the pulse generator code to run in parallel causing erroneous behavior
    EN pin handling was moved from IRQ to fixed time polling to eliminate this issue
    [CC_Charger.c, pulse_generator.c]
2024-01-31 Added pulse state tracking and short alert functionality
    [CC_Charger.c, pulse_generator.c]
2024-01-31 Updated pulse count code to output on PWM and actually increment
2024-02-01 Bug Fix
    Moved adding irq handler for pulse trip to init function, core no longer locks up
    [pulse_generator.c]
2024-02-05 Updated silkscreen and silkscreen file names.
2024-02-05 Minor modifications to silkscreen, Moved DPS logo to silkscreen.
2024-02-06 BOM and layout uptdates
    [CHARGER_POWER_STAGE.kicad_sch, SLOPE_GENERATION.kicad_sch]
2024-02-10 Fixed board clicking when enabled and no load connected
    Added a check before turning on the charger for the cap voltage. Don't limit duty cycle on turn on if cap voltage is above 35V. Don't turn on diode unless voltage is below 50V
    [CC_Charger.c, pulse_generator.c]
2024-02-15 Stabilized Code (Removed clicking eliminator and reduced output voltage)
    [pulse_generator.c]
2024-02-25 Layout Ready for Artwork
    [CHARGER_POWER_STAGE.kicad_sch, MICRO.kicad_sch]
2024-02-25 added silkscreen art to front and back of motherboard
2024-02-25 Manufacturing Files Generated
    [POWERCORE-V2.0_MOTHERBOARD-B_Cu.gbl, POWERCORE-V2.0_MOTHERBOARD-B_Mask.gbs, POWERCORE-V2.0_MOTHERBOARD-B_Paste.gbp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]
2024-02-29 Minor DRC corrections, regenerated Gerbers
    [POWERCORE-V2.0_MOTHERBOARD-B_Cu.gbl, POWERCORE-V2.0_MOTHERBOARD-B_Mask.gbs, POWERCORE-V2.0_MOTHERBOARD-B_Paste.gbp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]
2024-03-19 Updated pin settings for new board
2024-03-20 Modified Short Alert Behavior
    [pulse_generator.c]
2024-05-18 re-uploaded powercore photos
2024-05-18 uploaed powercore_front_drawing
2024-05-19 added manufacturing files from [24.04.10] batch
    [Powercore V2.0 Motherboard BoM.xlsx, Powercore V2.0 Motherboard Positions.xlsx]
2024-05-19 added CAD files for Powercore V2.0
    [Back Panel v18.3mf, Front Panel v45.3mf]
2024-05-19 added Powercore V2.0 STEP backup
2024-05-19 uploaded PDF schematic of Powercore V2.0 MB
2024-05-29 added HTML bill of material, and blacklisted non-populated components: C80, C46, R83, R68
2024-05-31 re-exported motherboard STEP file from KICAD
